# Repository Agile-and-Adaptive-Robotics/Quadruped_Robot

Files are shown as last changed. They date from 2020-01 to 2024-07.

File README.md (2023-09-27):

# AARL Quadruped Robot - Muscle Mutt

## Summary
This repository contains files relevant to the design, analysis, and testing of AARL's canine-inspired quadruped robot named Muscle Mutt.  Our goal in developing Muscle Mutt is for it to serve as a biologically relevant platform for testing embodied synthetic nervous systems pertaining to legged locomotion.  Toward this end, Muscle Mutt features body proportions similar to that of a Whippet, antagonistic pairs of braided pneumatic actuators (BPAs) that serve as proxies for muscles, and a CPG based neural control scheme.  All aspects of Muscle Mutt's design are under active development, including adjusting passive limb dynamics to be congruent with animal models, updating the electrical subsystem to incorporate a wider array of biologically relevant sensory feedback, and designing neural algorithms to generate stable and robust locomotion.

## References
More details on the design and testing of Muscle Mutt can be found in our associated papers.
```
@article{
C. W. Scharzenberger, “Design of a Canine Inspired Quadruped Robot as a Platform for Synthetic Neural Network Control,” Master’s Thesis, Portland State University, Digital, 2019. Accessed: Jun. 18, 2023. [Online]. Available: https://www.proquest.com/docview/2289587100?pq-origsite=gscholar&fromopenview=true
}
```
[Link to paper](https://pdxscholar.library.pdx.edu/cgi/viewcontent.cgi?article=6210&context=open_access_etds)

## Install Instructions
As a comprehensive robotics project, this repository contains information pertaining to three major areas of product development, including: (1) mechanical design, (2) electrical design, and (3) software.  The mechancial design for this project has been completed in Solidworks, while the electrical design has been completed in Eagle.  High level control software has primarily been developed in Matlab, though more recent efforts have been conducted in Python.  Requiste python modules are provided in requirement files in relevant directories.

## Repository Organization
This repository is organized into six primary directories, including: (1) Animatlab, (2) CAD_Electrical, (3) CAD_Mechanical, (4) Code, (5) Documentation, and (6) Manufacturing.  The names of these directories are largely self explanatory, with Animatlab neuromechanical simulations being stored in the Animatlab folder; Eagle CAD documents in the CAD_Electrical folder; Solidworks CAD documents in the CAD_Mechanical folder; Matlab, Python, and C code in the Code folder; supporting documentation and datasheets in the Documentation folder; and 3D printing documentation in the Manufacturing folder.

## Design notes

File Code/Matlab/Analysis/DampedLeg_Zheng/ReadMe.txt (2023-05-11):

FILE PATHS
Some folder names may have changed in an effort to clean up.
Data file and functions' locations may need to be re-established before running.

RAW DATA PROCESSING

Raw data files were too large to commit to GitHub but available upon request. 
Processed joint angle data is saved as Matlab data file "jdata".

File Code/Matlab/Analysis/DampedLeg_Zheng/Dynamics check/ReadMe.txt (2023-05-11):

OLD CODE
Contains troubleshooting code not actively used in analysis or old code that didn't work.

DYNAMICS CHECK CURRENT
Was used initially to create an animated display of a three link pendulum with given k,b,mu values

GEOMETRY CHECK
Was used in early phase of the project just to ensure center of masses and joint angles were defined correctly.

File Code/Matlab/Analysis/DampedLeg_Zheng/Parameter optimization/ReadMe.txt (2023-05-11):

DYNAMIC PROPERTIES CALC
Was used to calculate risetime in the hip, and frequency and damping ratio in the knee for rat trials so they did not need to be calculated at every iteration
Several different versions tried

IC_check
Main script is dynamic_IC_check.
Allows the user to enter values of friction (not used), k, and b.
User must enter a trial and muscle number to compare to.
Using IC from selected trial, ODE is run on system with selected parameters.
Joint angles over time are outputted and user has option to save. 

OPTIMIZER FUNCTIONS AND DATA
These are miscellaneous scripts need to run the optimizers.
Includes cost calculations, joint angle data, EOM, mechanical properties of the systems, etc.

OPTIMIZER SCRIPTS
Different optimization scripts
NOTE: Much of the code floating around this project has been copy and pasted from previous versions I've written, and some comments may contain errors
These had many changes and iterations, and the code gets a little sloppy in some places. Please contact me if there's any confusion.

RESULTS
Optimization results, sorted into folders.
Generally a data file and a figure are saved for each optimization.

TRIAL PLOTTING
Plotting of the rat leg trials used, as joint angle data over time.

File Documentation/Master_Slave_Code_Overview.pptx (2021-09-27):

## Master & Slave C Code Overview

March 25th, 2021

## Existing Hardware Organization

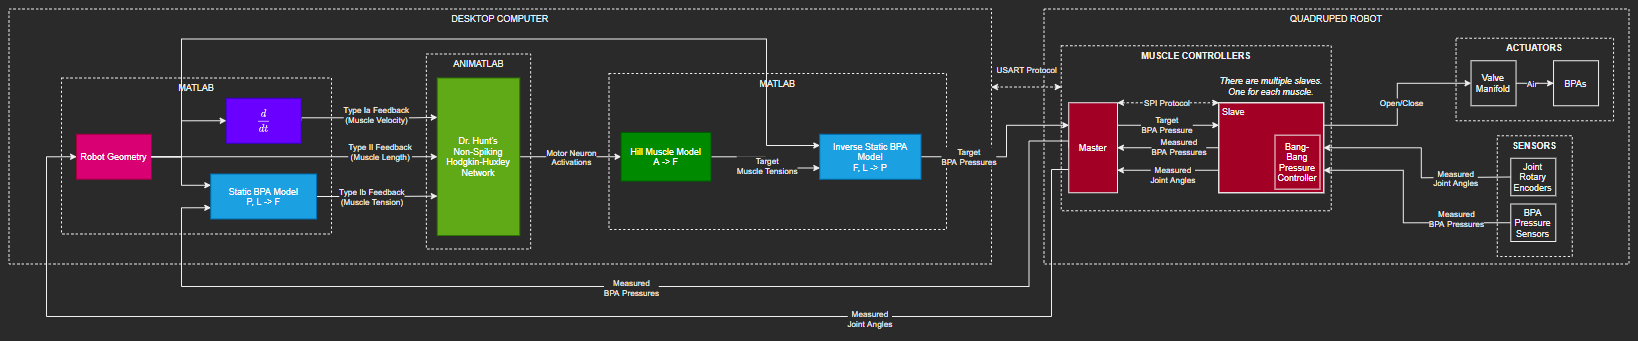
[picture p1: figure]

## Master Micro Duties

- Read desired muscle pressures from Matlab.
- Write desired muscle pressures to appropriate slave microcontrollers.
- Read sensor data from the slave microcontrollers.
- Write sensor data to Matlab.

## Master Micro approach

- Setup microcontroller in main function.
- In a timer interrupt, perform the required duties:
  - Read Matlab commands.
  - Write Slave commands.
  - Read Slave sensors.
  - Write Matlab sensors.
- Slave information is stored in a data structure: “slave manager”

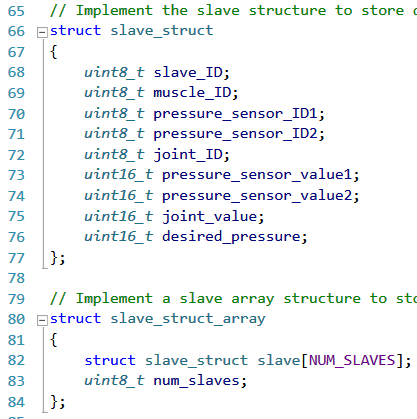
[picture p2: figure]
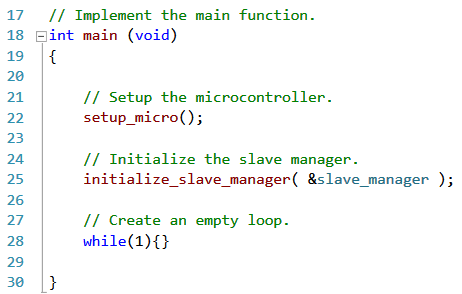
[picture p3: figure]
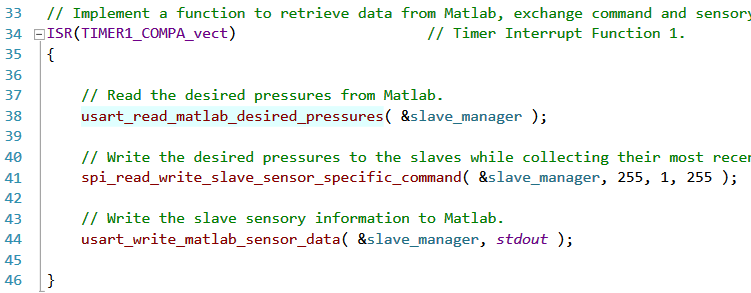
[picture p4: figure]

## A note about functions…

- Functions are stored in separate C files.
- Function files include:
  - Setup_Functions.c
  - SPI_Functions.c
  - USART_Functions.c
  - ADC_DAC_Functions.c
  - Conversion_Functions.c
  - Pin_Functions.c
  - Control Functions
  - Encoder Functions
- Master & Slave micros have their own versions of each of these files.

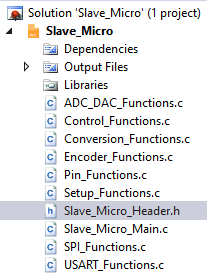
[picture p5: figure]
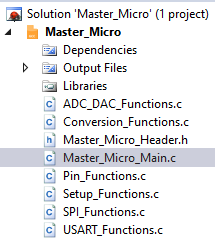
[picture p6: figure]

## Master Micro: Reading Matlab Commands

- Usart_read_matlab_desired_pressures
  - Waits for the “start sequence” from Matlab.
  - Reads the number of commands to expect.
  - Reads each set of command values.
  - Stores the desired pressure commands into the slave manager.

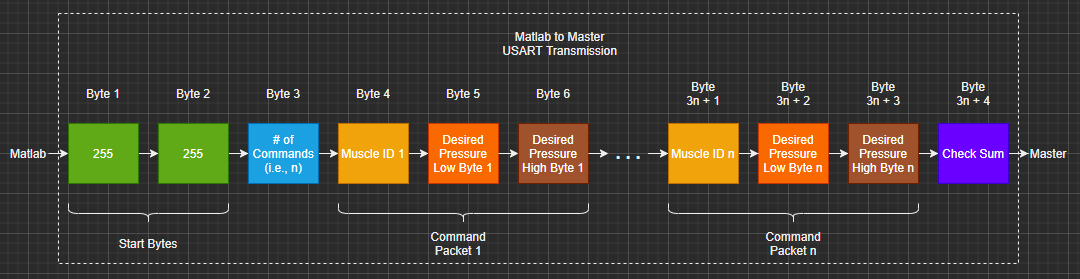
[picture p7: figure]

## Master Micro: Read / Write to Slaves

- Spi_read_write_slave_sensor_specific_command
  - Builds a byte array to send to the slave.
  - Writes the command ID.
  - Writes the sensor ID.
  - Writes the command low & high bytes.
  - Writes 4 more dummy bytes if we want to read all sensors from the slave.
  - Stores the received data in the slave manager.

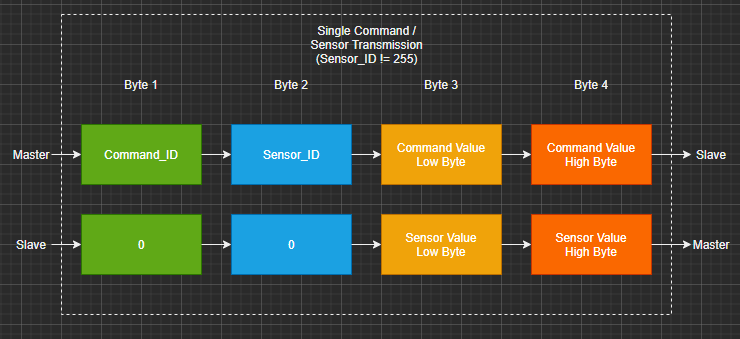
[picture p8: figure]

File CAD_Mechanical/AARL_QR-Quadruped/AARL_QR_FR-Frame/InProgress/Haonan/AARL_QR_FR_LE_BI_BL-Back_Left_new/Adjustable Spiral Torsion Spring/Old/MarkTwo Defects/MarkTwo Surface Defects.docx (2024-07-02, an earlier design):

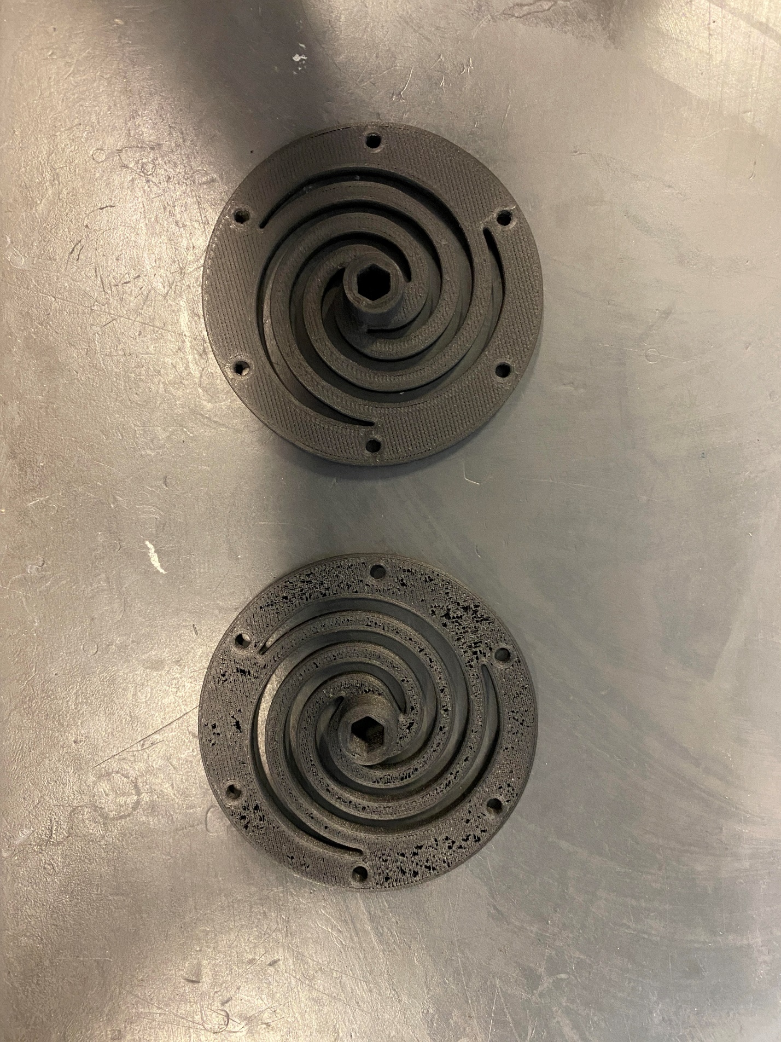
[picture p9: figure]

Top Surface

Mark Two

Onyx One

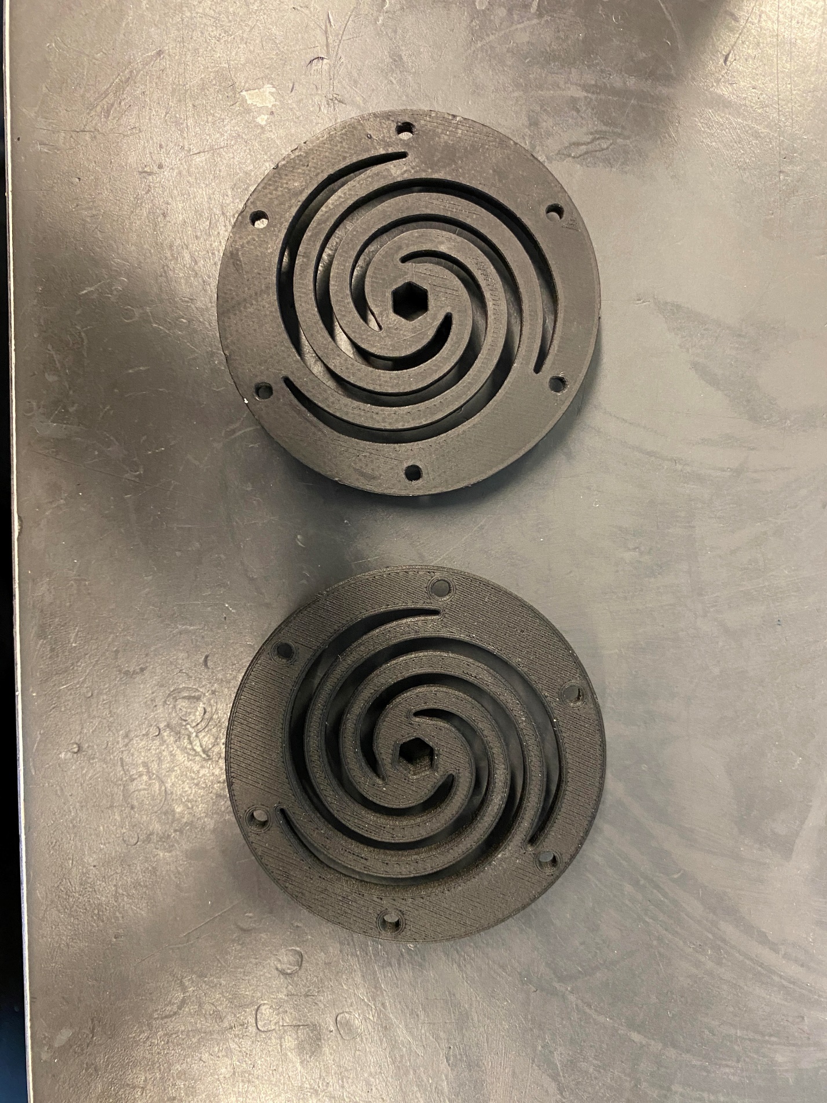
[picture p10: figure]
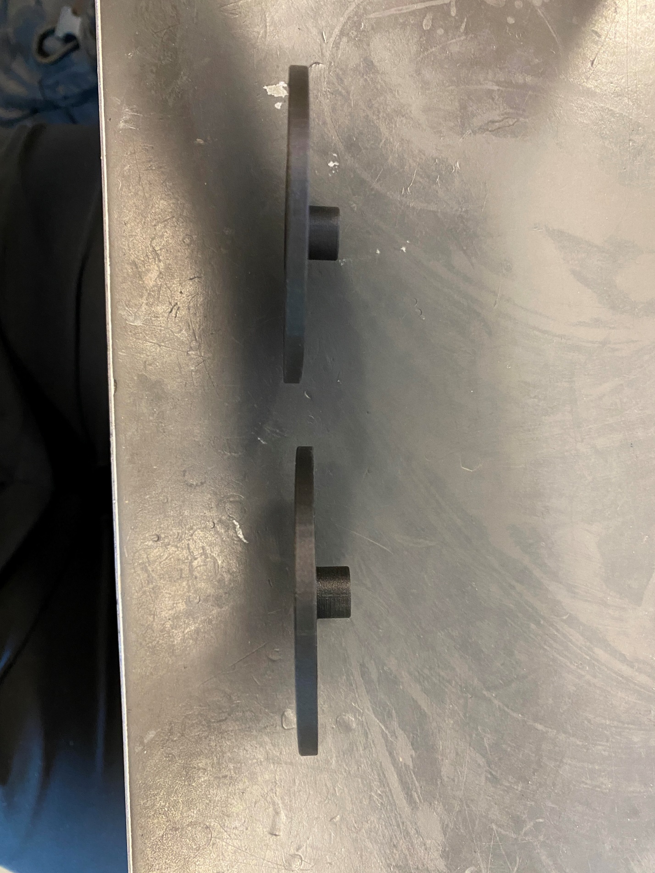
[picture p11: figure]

Bottom Surface

Onyx One

Mark Two

Side Walls

Mark Two

Onyx One

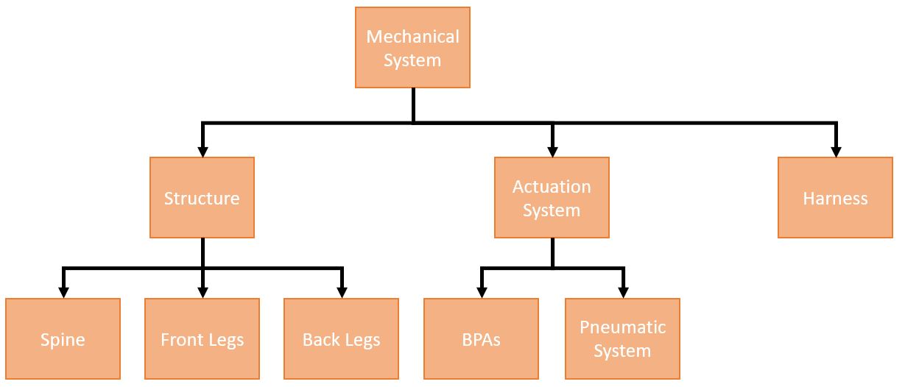
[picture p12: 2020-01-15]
Documentation/Pictures/PSU_Puppy_Pictures/Mechanical_Systems_Block_Diagram.JPG

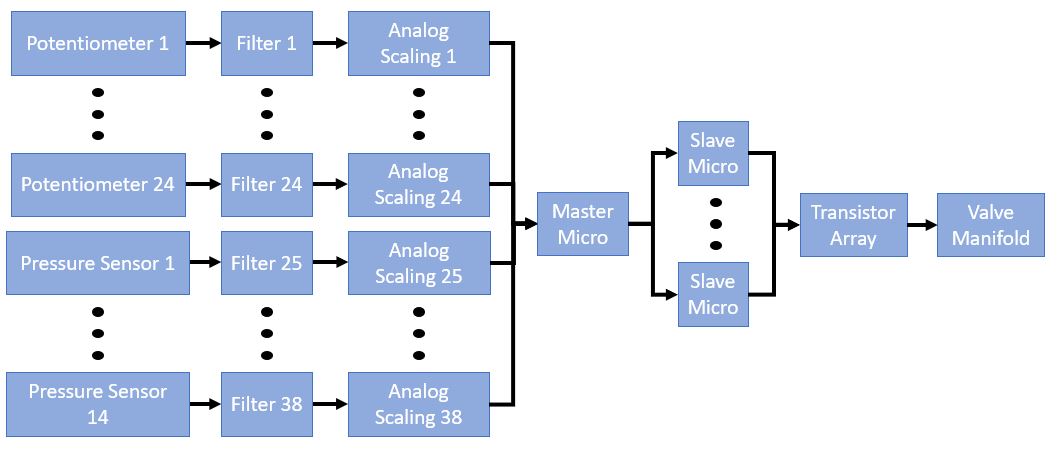
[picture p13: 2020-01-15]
Documentation/Pictures/PSU_Puppy_Pictures/Hardware_Flowchart.JPG

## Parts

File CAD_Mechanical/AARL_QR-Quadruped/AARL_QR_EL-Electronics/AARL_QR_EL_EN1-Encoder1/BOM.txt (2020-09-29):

3DX_CUI_DEVICES_Supplier: CUI Devices
3DX_CUI_DEVICES_Description: AMT10 Radial, Fixed Resolution, 500 PPR, Single Index Pulse, 4 mm Bore, Standard, Incremental, Capacitive Modular Encoder
3DX_CUI_DEVICES_Model Number: AMT102-0500-I4000-S

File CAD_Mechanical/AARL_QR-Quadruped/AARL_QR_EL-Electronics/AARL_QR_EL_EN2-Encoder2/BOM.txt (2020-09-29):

3DX_CUI_DEVICES_Supplier: CUI Devices
3DX_CUI_DEVICES_Description: AMT10 Radial, Fixed Resolution, 500 PPR, Single Index Pulse, 6.35 mm Bore, Standard, Incremental, Capacitive Modular Encoder
3DX_CUI_DEVICES_Model Number: AMT102-0500-I6350-S

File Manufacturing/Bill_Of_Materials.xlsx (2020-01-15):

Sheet: Bill Of Materials
ID | Name | Part # | Parent | Material Cost | Density | Unit Volume | Unit Mass | Unit Cost | Quantity | Total Mass | Total Cost | Quantity Owned | Quantity Needed | Manufacturing Method | Supplier | Link | Description | Notes
[#] | [-] | [-] | [-] | [$/cm^3] | [g/cm^3] | [cm^3/#] | [g/#] | [$/#] | [#] | [g] | [$] | [#] | [#] | [-] | [-] | [-] | [-] | [-]
1 | Center Cross Bar | AARL_Puppy_18_01_01_002 | Spine | 0.23625 | 1.2 | 24.4 | 29.28 | 5.7645 | 1 | 29.28 | 5.7645 | 0 | 1 | 3D Printing
2 | Front & Rear Cross Bar | AARL_Puppy_18_01_01_004 | Spine | 0.23625 | 1.2 | 18.2 | 21.84 | 4.29975 | 2 | 43.68 | 8.5995 | 0 | 2 | 3D Printing
3 | Front & Rear Cross Bar Insert | AARL_Puppy_18_01_01_005 | Spine | 0.23625 | 1.2 | 3.84 | 4.608 | 0.9072 | 4 | 18.432 | 3.6288 | 0 | 4 | 3D Printing
4 | Hip Potentiometer Bracket | AARL_Puppy_18_01_01_006 | Spine | 0.23625 | 1.2 | 6.48 | 7.776 | 1.5309 | 4 | 31.104 | 6.1236 | 0 | 4 | 3D Printing
5 | Middle Spine Section | AARL_Puppy_18_01_01_008 | Spine | 0.23625 | 1.2 | 258 | 309.6 | 60.9525 | 1 | 309.6 | 60.9525 | 0 | 1 | 3D Printing
6 | Outer Spine Section | AARL_Puppy_18_01_01_009 | Spine | 0.23625 | 1.2 | 224 | 268.8 | 52.92 | 2 | 537.6 | 105.84 | 0 | 2 | 3D Printing
7 | Ribbion Cable Bracket | AARL_Puppy_18_01_01_010 | Spine | 0.23625 | 1.2 | 9.39 | 11.268 | 2.2183875 | 1 | 11.268 | 2.2183875 | 0 | 1 | 3D Printing
8 | Air Supply Tubing Bracket | AARL_Puppy_18_01_01_011 | Spine | 0.23625 | 1.2 | 4.98 | 5.976 | 1.176525 | 1 | 5.976 | 1.176525 | 0 | 1 | 3D Printing
9 | Inside Piano Hinge Piece | AARL_Puppy_18_01_02_002 | Front Leg | 0.23625 | 1.2 | 5.74 | 6.888 | 1.356075 | 10 | 68.88 | 13.56075 | 0 | 10 | 3D Printing
10 | Standard Muscle Bracket (Small) | AARL_Puppy_18_01_02_003 | Front Leg | 0.23625 | 1.2 | 1.54 | 1.848 | 0.363825 | 18 | 33.264 | 6.54885 | 0 | 18 | 3D Printing
11 | Double Muscle Bracket (Center) | AARL_Puppy_18_01_02_005 | Front Leg | 0.23625 | 1.2 | 3.18 | 3.816 | 0.751275 | 2 | 7.632 | 1.50255 | 0 | 2 | 3D Printing
12 | Piano Hinge Potentiometer Piece | AARL_Puppy_18_01_02_009 | Front Leg | 0.23625 | 1.2 | 0.98 | 1.176 | 0.231525 | 10 | 11.76 | 2.31525 | 0 | 10 | 3D Printing
13 | Vishay Potentiometer | AARL_Puppy_18_01_02_013 | Electronics |  |  |  | 0 | 0 | 14 | 0 | 0 |  | 14 | Purchased | Vishay
14 | Bearing Insert | AARL_Puppy_18_01_02_014 | Front Leg | 0.23625 | 1.2 | 0.15 | 0.18 | 0.0354375 | 38 | 6.84 | 1.346625 | 0 | 38 | 3D Printing
15 | Outside Piano Hinge Piece | AARL_Puppy_18_01_02_015 | Front Leg | 0.23625 | 1.2 | 5.84 | 7.008 | 1.3797 | 10 | 70.08 | 13.797 | 0 | 10 | 3D Printing
16 | Foot Member | AARL_Puppy_18_01_02_016 | Front Leg | 0.23625 | 1.2 | 6.86 | 8.232 | 1.620675 | 4 | 32.928 | 6.4827 | 0 | 4 | 3D Printing
17 | Front Foot | AARL_Puppy_18_01_02_017 | Front Leg | 0.23625 | 1.2 | 4.2 | 5.04 | 0.99225 | 2 | 10.08 | 1.9845 | 0 | 2 | 3D Printing
18 | Back Hip Member | AARL_Puppy_18_01_02_018 | Front Leg | 0.23625 | 1.2 | 16.9 | 20.28 | 3.992625 | 2 | 40.56 | 7.98525 | 0 | 2 | 3D Printing
19 | Hip Potentiometer Piece | AARL_Puppy_18_01_02_021 | Front Leg | 0.23625 | 1.2 | 1.48 | 1.776 | 0.34965 | 4 | 7.104 | 1.3986 | 0 | 4 | 3D Printing
20 | Foot Cushioning Ball | AARL_Puppy_18_01_02_022 | Front Leg |  |  |  | 0 | 0 | 4 | 0 | 0 |  | 4 | Purchased
21 | Back Leg Double Short Double Bracket | AARL_Puppy_18_01_02_023 | Back Leg | 0.23625 | 1.2 | 3.3 | 3.96 | 0.779625 | 2 | 7.92 | 1.55925 | 0 | 2 | 3D Printing
22 | Back Leg Femur Member | AARL_Puppy_18_01_04_001 | Back Leg | 0.23625 | 1.2 | 22.08 | 26.496 | 5.2164 | 2 | 52.992 | 10.4328 | 0 | 2 | 3D Printing
23 | Back Leg Tibia Member | AARL_Puppy_18_01_04_011 | Back Leg | 0.23625 | 1.2 | 27.43 | 32.916 | 6.4803375 | 2 | 65.832 | 12.960675 | 0 | 2 | 3D Printing
24 | Back Foot | AARL_Puppy_18_01_04_017 | Back Leg | 0.23625 | 1.2 | 8.31 | 9.972 | 1.9632375 | 2 | 19.944 | 3.926475 | 0 | 2 | 3D Printing
25 | Back Leg Knee Bracket | AARL_Puppy_18_01_04_018 | Back Leg | 0.23625 | 1.2 | 8.29 | 9.948 | 1.9585125 | 2 | 19.896 | 3.917025 | 0 | 2 | 3D Printing
26 | Front Leg Femur Member | AARL_Puppy_18_01_06_001 | Front Leg | 0.23625 | 1.2 | 19.6 | 23.52 | 4.6305 | 2 | 47.04 | 9.261 | 0 | 2 | 3D Printing
27 | Front Leg Middle Member | AARL_Puppy_18_01_06_002 | Front Leg | 0.23625 | 1.2 | 23.4 | 28.08 | 5.52825 | 2 | 56.16 | 11.0565 | 0 | 2 | 3D Printing
28 | Front Leg Tibia | AARL_Puppy_18_01_06_004 | Front Leg | 0.23625 | 1.2 | 27.4 | 32.88 | 6.47325 | 2 | 65.76 | 12.9465 | 0 | 2 | 3D Printing
29 | Standard Muscle Bracket (Medium) | AARL_Puppy_18_01_06_005 | Front Leg | 0.23625 | 1.2 | 2.22 | 2.664 | 0.524475 | 6 | 15.984 | 3.14685 | 0 | 6 | 3D Printing
30 | Front Leg Pantograph Member | AARL_Puppy_18_01_06_006 | Front Leg | 0.23625 | 1.2 | 19 | 22.8 | 4.48875 | 2 | 45.6 | 8.9775 | 0 | 2 | 3D Printing
31 | Front Leg Double Knee Bracket | AARL_Puppy_18_01_06_008 | Front Leg | 0.23625 | 1.2 | 9.19 | 11.028 | 2.1711375 | 2 | 22.056 | 4.342275 | 0 | 2 | 3D Printing
32 | Front / Back Leg Knee Bracket | AARL_Puppy_18_01_06_010 | Front Leg | 0.23625 | 1.2 | 7.95 | 9.54 | 1.8781875 | 6 | 57.24 | 11.269125 | 0 | 6 | 3D Printing
33 | Front Hip Member | AARL_Puppy_18_01_06_011 | Front Leg | 0.23625 | 1.2 | 18.6 | 22.32 | 4.39425 | 2 | 44.64 | 8.7885 | 0 | 2 | 3D Printing
34 | Front Leg Top Offset Bracket | AARL_Puppy_18_01_06_012 | Front Leg | 0.23625 | 1.2 | 3.46 | 4.152 | 0.817425 | 2 | 8.304 | 1.63485 | 0 | 2 | 3D Printing
35 | Standard Potentiometer Mounting Bracket | AARL_Puppy_18_01_06_013 | Front Leg | 0.23625 | 1.2 | 2.45 | 2.94 | 0.5788125 | 10 | 29.4 | 5.788125 | 0 | 10 | 3D Printing
36 | Front Leg Bottom Offset Bracket | AARL_Puppy_18_01_06_014 | Front Leg | 0.23625 | 1.2 | 4.32 | 5.184 | 1.0206 | 2 | 10.368 | 2.0412 | 0 | 2 | 3D Printing
37 | Muscle String Tie Down | AARL_Puppy_18_01_09_004 | Muscle | 0.23625 | 1.2 | 2.27 | 2.724 | 0.5362875 | 24 | 65.376 | 12.8709 | 0 | 24 | 3D Printing
38 | Muscle Insert with Pneumatic Connection | AARL_Puppy_18_02_01_002 | Muscle | 0.23625 | 1.2 | 2.78 | 3.336 | 0.656775 | 24 | 80.064 | 15.7626 | 0 | 24 | 3D Printing
39 | QSML-M3-4 | AARL_Puppy_18_02_01_004 | Muscle |  |  |  | 0 | 0 | 24 | 0 | 0 |  | 24 | Purchased | Festo
40 | Hose Clamp | AARL_Puppy_18_02_01_005 | Pneumatics |  |  |  | 0 | 0 | 48 | 0 | 0 |  | 48 | Purchased
41 | Muscle Tie Down Insert | AARL_Puppy_18_02_01_007 | Muscle | 0.23625 | 1.2 | 2.53 | 3.036 | 0.5977125 | 24 | 72.864 | 14.3451 | 0 | 24 | 3D Printing
42 | VTUG-10-MRCR-S1TZ-26V20-T516-UL-M5S-12K | AARL_Puppy_18_02_31_000 | Pneumatics |  |  |  | 0 | 0 | 1 | 0 | 0 |  | 1 | Purchased | Festo
43 | QSL-G1/8-8 | AARL_Puppy_18_02_57_003 | Fitting |  |  |  | 0 | 0 | 1 | 0 | 0 |  | 1 | Purchased | Festo
44 | QSLV-M5-6 | AARL_Puppy_18_02_57_004 | Fitting |  |  |  | 0 | 0 | 1 | 0 | 0 |  | 1 | Purchased | Festo
45 | QSL-8 | AARL_Puppy_18_02_57_006 | Fitting |  |  |  | 0 | 0 | 1 | 0 | 0 |  | 1 | Purchased | Festo
46 | QSML-6 | AARL_Puppy_18_02_57_005 | Fitting |  |  |  | 0 | 0 | 1 | 0 | 0 |  | 1 | Purchased | Festo
47 | QSML-4 | AARL_Puppy_18_02_57_002 | Fitting |  |  |  | 0 | 0 | 48 | 0 | 0 |  | 48 | Purchased | Festo
48 | QSM-6-4 | AARL_Puppy_18_02_57_001 | Fitting |  |  |  | 0 | 0 | 24 | 0 | 0 |  | 24 | Purchased | Festo
49 | QSMT-4 | AARL_Puppy_18_02_57_007 | Fitting |  |  |  | 0 | 0 | 24 | 0 | 0 |  | 24 | Purchased | Festo
50 | Pressure Sensor Case | AARL_Puppy_18_03_03_001 | Electronics | 0.23625 | 1.2 | 109.88 | 131.856 | 25.95915 | 1 | 131.856 | 25.95915 | 0 | 1 | 3D Printing
51 | Pressure Sensor Case Lid | AARL_Puppy_18_03_03_002 | Electronics | 0.23625 | 1.2 | 40.22 | 48.264 | 9.501975 | 1 | 48.264 | 9.501975 | 0 | 1 | 3D Printing
52 | Pressure Sensor - MPX5700GP | AARL_Puppy_18_03_01_002 | Electronics |  |  |  | 0 | 0 | 24 | 0 | 0 |  | 24 | Purchased
53 | Solderable Breadboard | AARL_Puppy_18_03_01_009 | Electronics |  |  |  | 0 | 0 | 4 | 0 | 0 |  | 4 | Purchased
54 | Pressure Sensor Spacer | AARL_Puppy_18_03_01_010 | Electronics | 0.23625 | 1.2 | 0.09 | 0.108 | 0.0212625 | 48 | 5.184 | 1.0206 | 0 | 48 | 3D Printing
55 | Pressure Sensor Ribbon Cable Connector (46 Pin) | AARL_Puppy_18_03_05_002 | Electronics |  |  |  | 0 | 0 | 1 | 0 | 0 |  | 1 | Purchased
56 | Pressure Sensor Ribbon Cable (46 Pin) | AARL_Puppy_18_03_05_001 | Electronics |  |  |  | 0 | 0 | 2 | 0 | 0 |  | 2 | Purchased
57 | Electronics Input Connector |  | Electronics |  |  |  | 0 | 0 | 2 | 0 | 0 |  | 2 | Purchased |  |  |  | Still needs to be modeled.
58 | Electronics Input Ribbon Cable |  | Electronics |  |  |  | 0 | 0 | 2 | 0 | 0 |  | 2 | Purchased |  |  |  | Still needs to be modeled.
59 | #4-40x0.0625 Set Screw | AARL_Puppy_18_04_02_001 | Fastener |  |  |  | 0 | 0 | 28 | 0 | 0 |  | 28 | Purchased
60 | #4-40x0.25 SHCS | AARL_Puppy_18_04_01_004 | Fastener |  |  |  | 0 | 0 | 144 | 0 | 0 |  | 144 | Purchased
61 | #4-40x0.28125 SHCS | AARL_Puppy_18_04_01_005 | Fastener |  |  |  | 0 | 0 | 28 | 0 | 0 |  | 28 | Purchased
62 | #4-40x0.375 SHCS | AARL_Puppy_18_04_01_009 | Fastener |  |  |  | 0 | 0 | 18 | 0 | 0 |  | 18 | Purchased
63 | #4-40x2.5 SHCS | AARL_Puppy_18_04_01_014 | Fastener |  |  |  | 0 | 0 | 8 | 0 | 0 |  | 8 | Purchased
64 | #4-40 Nut | AARL_Puppy_18_04_07_002 | Fastener |  |  |  | 0 | 0 | 8 | 0 | 0 |  | 8 | Purchased
65 | #8-32x0.25 SHCS | AARL_Puppy_18_04_01_006 | Fastener |  |  |  | 0 | 0 | 38 | 0 | 0 |  | 38 | Purchased
66 | #8-32x0.75 SHCS | AARL_Puppy_18_04_01_007 | Fastener |  |  |  | 0 | 0 | 10 | 0 | 0 |  | 10 | Purchased
67 | #8-32x1.00 SHCS | AARL_Puppy_18_04_01_008 | Fastener |  |  |  | 0 | 0 | 4 | 0 | 0 |  | 4 | Purchased
68 | #8-32x1.25 SHSS | AARL_Puppy_18_04_01_013 | Fastener |  |  |  | 0 | 0 | 4 | 0 | 0 |  | 4 | Purchased
69 | 1/4-20x0.375 SHCS | AARL_Puppy_18_04_01_002 | Fastener |  |  |  | 0 | 0 | 6 | 0 | 0 |  | 6 | Purchased
70 | 1/4x0.75 Chicago Screw (Female) | AARL_Puppy_18_04_09_001 | Fastener |  |  |  | 0 | 0 | 52 | 0 | 0 |  | 52 | Purchased
71 | 1/4x0.75 Chicago Screw (Male) | AARL_Puppy_18_04_09_002 | Fastener |  |  |  | 0 | 0 | 52 | 0 | 0 |  | 52 | Purchased
72 | 1/4-20 Nut | AARL_Puppy_18_04_07_001 | Fastener |  |  |  | 0 | 0 | 14 | 0 | 0 |  | 14 | Purchased
73 | 1/8 ID Plastic Washer | AARL_Puppy_18_04_06_002 | Fastener |  |  |  | 0 | 0 | 16 | 0 | 0 |  | 16 | Purchased
74 | 3/32 Plastic Spacer | AARL_Puppy_18_04_06_001 | Fastener |  |  |  | 0 | 0 | 16 | 0 | 0 |  | 16 | Purchased
75 | 1/4 ID Roller Bearing | AARL_Puppy_18_04_03_001 | Fastener |  |  |  | 0 | 0 | 8 | 0 | 0 |  | 8 | Purchased
76 | String | AARL_Puppy_18_01_09_005 | Fastener |  |  |  | 0 | 0 | 1 | 0 | 0 |  | 1 | Purchased |  |  | 44.5322 inches required. | Many different models. No specific part number.
77 | M4 Tubing | AARL_Puppy_18_02_32_084 | Pneumatics |  |  |  | 0 | 0 | 1 | 0 | 0 |  | 1 | Purchased | Festo |  | 85.36159 feet required. | Many different models. No specific part number.
78 | M6 Tubing | AARL_Puppy_18_02_32_083 | Pneumatics |  |  |  | 0 | 0 | 1 | 0 | 0 |  | 1 | Purchased | Festo |  | 31.0577 inches required. | Many different models. No specific part number.
79 | M8 Tubing | AARL_Puppy_18_02_32_081 | Pneumatics |  |  |  | 0 | 0 | 1 | 0 | 0 |  | 1 | Purchased | Festo |  | 3.0571 inches required. | Many different models. No specific part number.
80 | Pneumatic Muscles | AARL_Puppy_18_02_33_001 | Pneumatics |  |  |  | 0 | 0 | 1 | 0 | 0 |  | 1 | Purchased | Festo |  | 122.875 inches required. | Many different models. No specific part number.
 |  |  |  |  |  |  |  |  |  | 2248.812

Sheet: Manufacturing Plan
Back Leg
ID | Name | Part # | Parent | Material Cost | Density | Unit Volume | Unit Mass | Unit Cost | Subassembly Quantity | Total Quantity | Total Mass | Total Cost | Notes
[#] | [-] | [-] | [-] | [$/cm^3] | [g/cm^3] | [cm^3/#] | [g/#] | [$/#] | [#] | [#] | [g] | [$] | [-]
1 | Single Muscle Bracket (Small) | AARL_Puppy_18_01_02_003 | Front Leg / Back Leg / Spine | 0.23625 | 1.2 | 1.54 | 1.848 | 0.363825 | 4 | 18 | 33.264 | 6.54885 | This part needs to be redesigned to avoid cracking down the middle where the mounting holes are located. Could potentially be replaced by the medium single muscle bracket.
2 | Single Muscle Bracket (Medium) | AARL_Puppy_18_01_06_005 | Front Leg / Back Leg | 0.23625 | 1.2 | 2.22 | 2.664 | 0.524475 | 1 | 6 | 15.984 | 3.14685
3 | Double Muscle Bracket (Short) | AARL_Puppy_18_01_02_023 | Back Leg | 0.23625 | 1.2 | 3.3 | 3.96 | 0.779625 | 1 | 2 | 7.92 | 1.55925
4 | Double Muscle Bracket (Medium) | AARL_Puppy_18_01_04_018 | Back Leg | 0.23625 | 1.2 | 8.29 | 9.948 | 1.9585125 | 1 | 2 | 19.896 | 3.917025
5 | Single Muscle Bracket (Long) | AARL_Puppy_18_01_06_010 | Front Leg / Back Leg | 0.23625 | 1.2 | 7.95 | 9.54 | 1.8781875 | 1 | 6 | 57.24 | 11.269125
6 | Standard Potentiometer Mounting Bracket | AARL_Puppy_18_01_06_013 | Front Leg / Back Leg | 0.23625 | 1.2 | 2.45 | 2.94 | 0.5788125 | 2 | 10 | 29.4 | 5.788125
7 | Hip Potentiometer Piece | AARL_Puppy_18_01_02_021 | Front Leg / Back Leg | 0.23625 | 1.2 | 1.48 | 1.776 | 0.34965 | 1 | 4 | 7.104 | 1.3986
8 | Bearing Insert | AARL_Puppy_18_01_02_014 | Front Leg / Back Leg | 0.23625 | 1.2 | 0.15 | 0.18 | 0.0354375 | 9 | 38 | 6.84 | 1.346625
9 | Inside Piano Hinge Piece | AARL_Puppy_18_01_02_002 | Front Leg / Back Leg | 0.23625 | 1.2 | 5.74 | 6.888 | 1.356075 | 2 | 10 | 68.88 | 13.56075
10 | Outside Piano Hinge Piece | AARL_Puppy_18_01_02_015 | Front Leg / Back Leg | 0.23625 | 1.2 | 5.84 | 7.008 | 1.3797 | 2 | 10 | 70.08 | 13.797
11 | Piano Hinge Potentiometer Piece | AARL_Puppy_18_01_02_009 | Front Leg / Back Leg | 0.23625 | 1.2 | 0.98 | 1.176 | 0.231525 | 2 | 10 | 11.76 | 2.31525
12 | Back Hip Member | AARL_Puppy_18_01_02_018 | Back Leg | 0.23625 | 1.2 | 16.9 | 20.28 | 3.992625 | 1 | 2 | 40.56 | 7.98525
13 | Back Leg Femur Member | AARL_Puppy_18_01_04_001 | Back Leg | 0.23625 | 1.2 | 22.08 | 26.496 | 5.2164 | 1 | 2 | 52.992 | 10.4328
14 | Back Leg Tibia Member | AARL_Puppy_18_01_04_011 | Back Leg | 0.23625 | 1.2 | 27.43 | 32.916 | 6.4803375 | 1 | 2 | 65.832 | 12.960675
15 | Foot Member | AARL_Puppy_18_01_02_016 | Front Leg / Back Leg | 0.23625 | 1.2 | 6.86 | 8.232 | 1.620675 | 1 | 4 | 32.928 | 6.4827
16 | Back Foot | AARL_Puppy_18_01_04_017 | Back Leg | 0.23625 | 1.2 | 8.31 | 9.972 | 1.9632375 | 1 | 2 | 19.944 | 3.926475 | This part may be too long and weak.
Front Leg
ID | Name | Part # | Parent | Material Cost | Density | Unit Volume | Unit Mass | Unit Cost | Subassembly Quantity | Total Quantity | Total Mass | Total Cost | Notes
[#] | [-] | [-] | [-] | [$/cm^3] | [g/cm^3] | [cm^3/#] | [g/#] | [$/#] | [#] | [#] | [g] | [$] | [-]
1 | Single Muscle Bracket (Small) | AARL_Puppy_18_01_02_003 | Front Leg / Back Leg / Spine | 0.23625 | 1.2 | 1.54 | 1.848 | 0.363825 | 3 | 18 | 33.264 | 6.54885
2 | Single Muscle Bracket (Medium) | AARL_Puppy_18_01_06_005 | Front Leg / Back Leg | 0.23625 | 1.2 | 2.22 | 2.664 | 0.524475 | 2 | 6 | 15.984 | 3.14685
3 | Single Muscle Bracket (Long) | AARL_Puppy_18_01_06_010 | Front Leg / Back Leg | 0.23625 | 1.2 | 7.95 | 9.54 | 1.8781875 | 2 | 6 | 57.24 | 11.269125
4 | Standard Potentiometer Mounting Bracket | AARL_Puppy_18_01_06_013 | Front Leg / Back Leg | 0.23625 | 1.2 | 2.45 | 2.94 | 0.5788125 | 3 | 10 | 29.4 | 5.788125
5 | Hip Potentiometer Piece | AARL_Puppy_18_01_02_021 | Front Leg / Back Leg | 0.23625 | 1.2 | 1.48 | 1.776 | 0.34965 | 1 | 4 | 7.104 | 1.3986
6 | Bearing Insert | AARL_Puppy_18_01_02_014 | Front Leg / Back Leg | 0.23625 | 1.2 | 0.15 | 0.18 | 0.0354375 | 11 | 38 | 6.84 | 1.346625
7 | Inside Piano Hinge Piece | AARL_Puppy_18_01_02_002 | Front Leg / Back Leg | 0.23625 | 1.2 | 5.74 | 6.888 | 1.356075 | 3 | 10 | 68.88 | 13.56075
8 | Outside Piano Hinge Piece | AARL_Puppy_18_01_02_015 | Front Leg / Back Leg | 0.23625 | 1.2 | 5.84 | 7.008 | 1.3797 | 3 | 10 | 70.08 | 13.797
9 | Piano Hinge Potentiometer Piece | AARL_Puppy_18_01_02_009 | Front Leg / Back Leg | 0.23625 | 1.2 | 0.98 | 1.176 | 0.231525 | 3 | 10 | 11.76 | 2.31525
10 | Foot Member | AARL_Puppy_18_01_02_016 | Front Leg / Back Leg | 0.23625 | 1.2 | 6.86 | 8.232 | 1.620675 | 1 | 4 | 32.928 | 6.4827
11 | Double Muscle Bracket (Long) | AARL_Puppy_18_01_06_008 | Front Leg | 0.23625 | 1.2 | 9.19 | 11.028 | 2.1711375 | 1 | 2 | 22.056 | 4.342275
12 | Front Leg Top Offset Bracket | AARL_Puppy_18_01_06_012 | Front Leg | 0.23625 | 1.2 | 3.46 | 4.152 | 0.817425 | 1 | 2 | 8.304 | 1.63485
13 | Front Leg Bottom Offset Bracket | AARL_Puppy_18_01_06_014 | Front Leg | 0.23625 | 1.2 | 4.32 | 5.184 | 1.0206 | 1 | 2 | 10.368 | 2.0412
14 | Front Hip Member | AARL_Puppy_18_01_06_011 | Front Leg | 0.23625 | 1.2 | 18.6 | 22.32 | 4.39425 | 1 | 2 | 44.64 | 8.7885
15 | Front Leg Femur Member | AARL_Puppy_18_01_06_001 | Front Leg | 0.23625 | 1.2 | 19.6 | 23.52 | 4.6305 | 1 | 2 | 47.04 | 9.261
16 | Front Leg Middle Member | AARL_Puppy_18_01_06_002 | Front Leg | 0.23625 | 1.2 | 23.4 | 28.08 | 5.52825 | 1 | 2 | 56.16 | 11.0565
17 | Front Leg Tibia | AARL_Puppy_18_01_06_004 | Front Leg | 0.23625 | 1.2 | 27.4 | 32.88 | 6.47325 | 1 | 2 | 65.76 | 12.9465
18 | Front Leg Pantograph Member | AARL_Puppy_18_01_06_006 | Front Leg | 0.23625 | 1.2 | 19 | 22.8 | 4.48875 | 1 | 2 | 45.6 | 8.9775
19 | Front Foot | AARL_Puppy_18_01_02_017 | Front Leg | 0.23625 | 1.2 | 4.2 | 5.04 | 0.99225 | 1 | 2 | 10.08 | 1.9845
Muscles
ID | Name | Part # | Parent | Material Cost | Density | Unit Volume | Unit Mass | Unit Cost | Subassembly Quantity | Total Quantity | Total Mass | Total Cost | Notes
[#] | [-] | [-] | [-] | [$/cm^3] | [g/cm^3] | [cm^3/#] | [g/#] | [$/#] | [#] | [#] | [g] | [$] | [-]
1 | Muscle String Tie Down | AARL_Puppy_18_01_09_004 | Muscle | 0.23625 | 1.2 | 2.27 | 2.724 | 0.5362875 | 1 | 24 | 65.376 | 12.8709 | Make string holes larger.
2 | Muscle Insert with Pneumatic Connection | AARL_Puppy_18_02_01_002 | Muscle | 0.23625 | 1.2 | 2.78 | 3.336 | 0.656775 | 1 | 24 | 80.064 | 15.7626
3 | Muscle Tie Down Insert | AARL_Puppy_18_02_01_007 | Muscle | 0.23625 | 1.2 | 2.53 | 3.036 | 0.5977125 | 1 | 24 | 72.864 | 14.3451 | Make string holes larger.
Electronics Housing
ID | Name | Part # | Parent | Material Cost | Density | Unit Volume | Unit Mass | Unit Cost | Subassembly Quantity | Total Quantity | Total Mass | Total Cost | Notes
[#] | [-] | [-] | [-] | [$/cm^3] | [g/cm^3] | [cm^3/#] | [g/#] | [$/#] | [#] | [#] | [g] | [$] | [-]
1 | Pressure Sensor Case | AARL_Puppy_18_03_03_001 | Electronics | 0.23625 | 1.2 | 109.88 | 131.856 | 25.95915 | 1 | 1 | 131.856 | 25.95915 | Move screw holes for lid mounting in to give them more meat.
2 | Pressure Sensor Case Lid | AARL_Puppy_18_03_03_002 | Electronics | 0.23625 | 1.2 | 40.22 | 48.264 | 9.501975 | 1 | 1 | 48.264 | 9.501975 | Move screw holes for lid mounting in to give them more meat.
3 | Pressure Sensor Spacer | AARL_Puppy_18_03_01_010 | Electronics | 0.23625 | 1.2 | 0.09 | 0.108 | 0.0212625 | 48 | 48 | 5.184 | 1.0206 | Move screw holes for lid mounting in to give them more meat.
Spine
ID | Name | Part # | Parent | Material Cost | Density | Unit Volume | Unit Mass | Unit Cost | Subassembly Quantity | Total Quantity | Total Mass | Total Cost | Notes
[#] | [-] | [-] | [-] | [$/cm^3] | [g/cm^3] | [cm^3/#] | [g/#] | [$/#] | [#] | [#] | [g] | [$] | [-]
1 | Single Muscle Bracket (Small) | AARL_Puppy_18_01_02_003 | Front Leg / Back Leg / Spine | 0.23625 | 1.2 | 1.54 | 1.848 | 0.363825 | 4 | 18 | 33.264 | 6.54885
1 | Double Muscle Bracket (Short) | AARL_Puppy_18_01_02_005 | Spine | 0.23625 | 1.2 | 3.18 | 3.816 | 0.751275 | 2 | 2 | 7.632 | 1.50255
9 | Air Supply Tubing Bracket | AARL_Puppy_18_01_01_011 | Spine | 0.23625 | 1.2 | 4.98 | 5.976 | 1.176525 | 1 | 1 | 5.976 | 1.176525
2 | Ribbion Cable Bracket | AARL_Puppy_18_01_01_010 | Spine | 0.23625 | 1.2 | 9.39 | 11.268 | 2.2183875 | 1 | 1 | 11.268 | 2.2183875 | Too fragile to bending. Need support material to prevent bending.
3 | Center Cross Bar | AARL_Puppy_18_01_01_002 | Spine | 0.23625 | 1.2 | 24.4 | 29.28 | 5.7645 | 1 | 1 | 29.28 | 5.7645
4 | Front & Rear Cross Bar | AARL_Puppy_18_01_01_004 | Spine | 0.23625 | 1.2 | 18.2 | 21.84 | 4.29975 | 2 | 2 | 43.68 | 8.5995
5 | Front & Rear Cross Bar Insert | AARL_Puppy_18_01_01_005 | Spine | 0.23625 | 1.2 | 3.84 | 4.608 | 0.9072 | 4 | 4 | 18.432 | 3.6288
6 | Hip Potentiometer Bracket | AARL_Puppy_18_01_01_006 | Spine | 0.23625 | 1.2 | 6.48 | 7.776 | 1.5309 | 4 | 4 | 31.104 | 6.1236
7 | Middle Spine Section | AARL_Puppy_18_01_01_008 | Spine | 0.23625 | 1.2 | 258 | 309.6 | 60.9525 | 1 | 1 | 309.6 | 60.9525
8 | Outer Spine Section | AARL_Puppy_18_01_01_009 | Spine | 0.23625 | 1.2 | 224 | 268.8 | 52.92 | 2 | 2 | 537.6 | 105.84

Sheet: Inventory
ID | Name | Part # | Parent | Quantity Owned | Supplier | Notes | Link
[#] | [-] | [-] | [-] | [#] | [-] | [-] | [-]
1 | Size 1'' Oetiker Stepless Ear Clamps, Single Ear Hose Clamps | AARL_Puppy_18_02_01_005 | Pneumatics | 10 | Murray |  | https://www.murraycorp.com/products/clamps/?_vsrefdom=ppcgoogle
2 | 1 3/16'' Cambridge Standard Hose Clamps | AARL_Puppy_18_02_01_005 | Pneumatics | 20 | Cambridge |  | http://www.cambridgeresources.com/products/c-12-standardhoseclamps/p-274-series2300
3 | One Ear Oetiker Clamp 133 for 7/16 OD Hose | AARL_Puppy_18_02_01_005 | Pneumatics | 46 | Murray |  | https://www.homebrewing.org/One-Ear-Oetiker-Clamp-133-Size-For-716-OD-Hose--100-Count_p_917.html
4 | Oetiker 15.7mm Clamp | AARL_Puppy_18_02_01_005 | Pneumatics | 3 | Murray |  | https://www.amazon.com/Oetiker-Stepless%C2%AE-Clamps-Single-Available/dp/B00ZJFWAK4
5 | Breeze Hose Clamp (Small) | AARL_Puppy_18_02_01_005 | Pneumatics | 26 | Breeze |  | http://www.breezehoseclamps.com/breeze/mini/
6 | M8 Tubing | AARL_Puppy_18_02_32_081 | Pneumatics | 1 | Festo | 3.0571 inches required. Estimated ~100 feet owned. Order Code: PUN-8X1,25-SI
7 | 1/4 Tubing |  | Pneumatics | 2 |  | ~100 feet each.
8 | 6mm x R1/4 Nitra Straight Fitting |  | Fitting | 20 | Nitra |  | https://www.automationdirect.com/adc/Overview/Catalog/Pneumatic_Components/Push-to-Connect_R-Thread_Pneumatic_Fittings_(Thermoplastic)/Male_Straight_(Round_Bo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
9 | Urbest ~6mm x ? Threaded Straight Fitting |  | Fitting | 20 | Urbest
10 | 1/4 x 5/16 Straight Fitting |  | Fitting | 5 | Mettle Air
11 | 1/4 T Fitting |  | Fitting | 20 | HFX
12 | 1/4 Y Fitting |  | Fitting | 20 | HFX
13 | 1/4 x 5/16? Thread L Fitting |  | Fitting | 3 | Mettle Air
14 | M4? Thread x 1/4 Straight Fitting |  | Fitting | 6 | Mettle Air
15 | POT 100 kOhm 1/5W Plastic Linear |  | Electronics | 25 | Digikey
16 | Pressure Sensor - MPX5700GP | AARL_Puppy_18_03_01_002 | Electronics | 32 | Digikey
17 | 1/4-20 Nut | AARL_Puppy_18_04_07_001 | Fastener | 25 | Digikey
18 | String | AARL_Puppy_18_01_09_005 | Fastener | 1 |  | 44.5322 inches required.

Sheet: Purchase Plan
ID | Name | Part # | Parent | Unit Cost | Quantity | Total Cost | Supplier | Notes | Link
[#] | [-] | [-] | [-] | [$/#] | [#] | [$] | [-] | [-] | [-]
1 | Foot Cushioning Ball | AARL_Puppy_18_01_02_022 | Front Leg |  | 4 | 0
2 | VTUG-10-MRCR-S1TZ-26V20-Q8LA-UL-M5S-12K | AARL_Puppy_18_02_31_000, Needs to be updated for new fitting sizes. | Pneumatics | 1505.86 | 1 | 1505.86 | Festo | Order Code: VTUG-10-MRCR-S1TZ-26V20-Q8LA-UL-M5S-12K | https://www.festo.com/cat/en-us_us/products_VTUG | Could get this later.
3 | M4 Tubing | AARL_Puppy_18_02_32_084 | Pneumatics | 36.5 | 1 | 36.5 | Festo | Order Code: PUN-4X0,75-SI, 50m Pack | https://www.festo.com/cat/en-us_us/products_PUN
4 | QSML-M3-4 | AARL_Puppy_18_02_01_004, Needs to be updated from M3 to M5. | Fitting | 45.8 | 3 | 137.4 | Festo | Order Code: QSML-M3-4, 10 Pc. Pack | https://www.festo.com/cat/en-us_us/products_QSM
5 | QSL-G1/8-8 | AARL_Puppy_18_02_57_003 | Fitting | 3.67 | 1 | 3.67 | Festo | Order Code: QSL-G1/8-8, each | https://www.festo.com/cat/en-us_us/products_QS
6 | QSLV-M5-6 | AARL_Puppy_18_02_57_004 | Fitting | 4.36 | 1 | 4.36 | Festo | Order Code: QSLV-M5-6, each | https://www.festo.com/cat/en-us_us/products_QS
7 | QSL-8 | AARL_Puppy_18_02_57_006 | Fitting | 35.2 | 1 | 35.2 | Festo | Order Code: QSL-8, 10 Pc. Pack | https://www.festo.com/cat/en-us_us/products_QS
8 | QSML-6 | AARL_Puppy_18_02_57_005 | Fitting | 30.7 | 1 | 30.7 | Festo | Order Code: QSML-6, 10 Pc. Pack | https://www.festo.com/cat/en-us_us/products_QSM
9 | QSML-4 | AARL_Puppy_18_02_57_002 | Fitting | 29.2 | 5 | 146 | Festo | Order Code: QSML-4, 10 Pc. Pack | https://www.festo.com/cat/en-us_us/products_QSM
10 | QSM-6-4 | AARL_Puppy_18_02_57_001 | Fitting | 31.6 | 3 | 94.8 | Festo | Order Code: QSM-6-4, 10 Pc. Pack | https://www.festo.com/cat/en-us_us/products_QSM
11 | QSMT-4 | AARL_Puppy_18_02_57_007 | Fitting | 38.1 | 3 | 114.3 | Festo | Order Code: QSMT-4, 10 Pc. Pack | https://www.festo.com/cat/en-us_us/products_QSM
12 | 1/4x0.75 Chicago Screw (Female) | AARL_Puppy_18_04_09_001 | Fastener | 1.81 | 52 | 94.12 | McMaster-Carr | Order Code: 99637A305, each | https://www.mcmaster.com/99637a305 | or this
13 | 1/8 ID Plastic Washer | AARL_Puppy_18_04_06_002 | Fastener | 8.24 | 1 | 8.24 | McMaster-Carr | Order Code: 90295A370, 100 Pc. Pack | https://www.mcmaster.com/90295a370
14 | 3/32 Plastic Spacer | AARL_Puppy_18_04_06_001 | Fastener | 2.29 | 1 | 2.29 | McMaster-Carr | Order Code: 90176A102, 25 Pc. Pack | https://www.mcmaster.com/90176a102
15 | 1/4 ID Roller Bearing | AARL_Puppy_18_04_03_001 | Fastener | 5.98 | 8 | 47.84 | McMaster-Carr | Order Code: 60355K503, each | https://www.mcmaster.com/60355k503 | Either this
16 | 3/16 ID Roller Bearing |  | Fastener | 6.9 | 8 | 55.2 | McMaster-Carr | Order Code: 60355K502, each | https://www.mcmaster.com/60355k502 | or this
17 | VTUG-10-MRCR-S1T-26V20-T516LA-UL-T532S-12K |  | Pneumatics | 1556.66 | 1 | 1556.66 | Festo | each | https://www.festo.com/cat/en-us_us/products_VTUG
18 | QBL-M5-5/32-U-M |  | Fitting | 31.5 | 3 | 94.5 | Festo | 10 Pc. Pack | https://www.festo.com/cat/en-us_us/products_QB
19 | QBML-5/32T-U |  | Fitting | 29.4 | 5 | 147 | Festo | 10 Pc. Pack | https://www.festo.com/cat/en-us_us/products_QB
20 | QBMT-5/32T-U |  | Fitting | 40.3 | 3 | 120.9 | Festo | 10 Pc. Pack | https://www.festo.com/cat/en-us_us/products_QB
21 | QBM-1/4T-5/32-U |  | Fitting | 31 | 3 | 93 | Festo | 10 Pc. Pack | https://www.festo.com/cat/en-us_us/products_QB
22 | 5/32 OD Tubing |  | Pneumatics | 18.3 | 1 | 18.3 | ATP | 250 ft pack | https://www.atp4pneumatics.com/product/pe04m-532bbk/
23 | MTL 5/32-U10 |  | Fitting | 0.99 | 24 | 23.76 | Mettle Air | each | https://www.mettleair.com/store/ptc/threaded-main/male-elbow/mtl-ixnpt/push-to-connect-90-elbow-fitting-5-32-od-10-32-unf-male.html
24 | MTV 5/32 |  | Fitting | 0.91 | 48 | 43.68 | Mettle Air | each | https://www.mettleair.com/store/ptc/unions-main/push-to-connect-elbow-union-5-32-od-5-32-od.html
25 | MTE 5/32-5/32 |  | Fitting | 1.33 | 24 | 31.92 | Mettle Air | each | https://www.mettleair.com/store/ptc/unions-main/mte-main/push-to-connect-tee-union-5-32-od-5-32-od.html
26 | MTU 1/4-5/32 |  | Fitting | 1.02 | 24 | 24.48 | Mettle Air | each | https://www.mettleair.com/store/ptc/unions-main/mtu-main/mtu-imp/push-to-connect-straight-union-reducer-1-4-od-5-32-od.html
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

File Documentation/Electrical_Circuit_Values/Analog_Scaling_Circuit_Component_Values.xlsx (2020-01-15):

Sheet: FA2019_FrontLeftLeg
ID | Name | Pressure Sensor |  | Potentiometer
 |  | Value | Suffix | Value | Suffix
[#] | [-] | [Ohm] | [-] | [Ohm] | [-]
1 | R1 | 3.3 | k | 33 | k
2 | R2 | 3.3 | k | 39 | k
3 | R3 | 4.7 | k | 18 | k
4 | R4 | 4.7 | k | 18 | k
5 | R5 | 3.3 | k | 39 | k
6 | R6 | 33 | k | 10 | k
7 | R7 | 3.3 | k | 33 | k
8 | R8 | 33 | k | 47 | k
9 | R9 | 4.7 | k | 18 | k
10 | R10 | 5.6 | k | 8.2 | k
11 | R11 | 4.7 | k | 18 | k
12 | R12 | 5.6 | k | 15 | k
13 | R13 | 4.7 | k | 10 | k
14 | R14 | 5.6 | k | 39 | k
15 | R15 | 4.7 | k | 12 | k
16 | R16 | 5.6 | k | 12 | k
17 | R17 | 3.3 | k | 15 | k
18 | R18 | 33 | k | 22 | k
19 | R19 | 3.3 | k | 22 | k
20 | R20 | 33 | k | 33 | k
21 | R21 | 3.3 | k | 15 | k
22 | R22 | 4.7 | k | 10 | k
23 | R23 | 4.7 | k | 12 | k
24 | R24 | 3.3 | k | 22 | k

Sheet: FA2019_BackLeftLeg
ID | Unit | Board | Channel | Front / Back | Left / Right | Joint | Muscle Type | Sensor Type | Name | Value | Suffix | Value | Quantity
[#] | [#] | [#] | [#] | [-] | [-] | [-] | [-] | [-] | [-] | [Ohm] | [-] | [Ohm] | [#]
1 | 1 | 1 | 0 | Front | Left | Hip | Ext | Pressure | R2 | 3.3 | k | 1.2 | 18
2 | 1 | 1 | 0 | Front | Left | Hip | Ext | Pressure | R3 | 4.7 | k | 1.5 | 18
3 | 1 | 1 | 0 | Front | Left | Hip | Ext | Pressure | R5 | 3.3 | k | 3.3 | 20
4 | 1 | 1 | 0 | Front | Left | Hip | Ext | Pressure | R9 | 4.7 | k | 4.7 | 12
5 | 1 | 1 | 0 | Front | Left | Hip | Ext | Pressure | R6 | 33 | k | 5.6 | 8
6 | 1 | 1 | 0 | Front | Left | Hip | Ext | Pressure | R10 | 5.6 | k | 6.8 | 2
7 | 1 | 1 | 1 | Front | Left | Hip | Flx | Pressure | R21 | 3.3 | k | 8.2 | 1
8 | 1 | 1 | 1 | Front | Left | Hip | Flx | Pressure | R22 | 4.7 | k | 10 | 4
9 | 1 | 1 | 1 | Front | Left | Hip | Flx | Pressure | R17 | 3.3 | k | 15 | 8
10 | 1 | 1 | 1 | Front | Left | Hip | Flx | Pressure | R13 | 4.7 | k | 18 | 19
11 | 1 | 1 | 1 | Front | Left | Hip | Flx | Pressure | R18 | 33 | k | 22 | 14
12 | 1 | 1 | 1 | Front | Left | Hip | Flx | Pressure | R14 | 5.6 | k | 27 | 14
13 | 1 | 1 | 2 | Front | Left | Knee | Ext | Pressure | R1 | 3.3 | k | 33 | 23
14 | 1 | 1 | 2 | Front | Left | Knee | Ext | Pressure | R4 | 4.7 | k | 39 | 5
15 | 1 | 1 | 2 | Front | Left | Knee | Ext | Pressure | R7 | 3.3 | k | 47 | 10
16 | 1 | 1 | 2 | Front | Left | Knee | Ext | Pressure | R11 | 4.7 | k | 560 | 9
17 | 1 | 1 | 2 | Front | Left | Knee | Ext | Pressure | R8 | 33 | k
18 | 1 | 1 | 2 | Front | Left | Knee | Ext | Pressure | R12 | 5.6 | k
19 | 1 | 1 | 3 | Front | Left | Knee | Flx | Pressure | R24 | 3.3 | k
20 | 1 | 1 | 3 | Front | Left | Knee | Flx | Pressure | R23 | 4.7 | k
21 | 1 | 1 | 3 | Front | Left | Knee | Flx | Pressure | R19 | 3.3 | k
22 | 1 | 1 | 3 | Front | Left | Knee | Flx | Pressure | R15 | 4.7 | k
23 | 1 | 1 | 3 | Front | Left | Knee | Flx | Pressure | R20 | 33 | k
24 | 1 | 1 | 3 | Front | Left | Knee | Flx | Pressure | R16 | 5.6 | k
25 | 1 | 2 | 0 | Front | Left | Ankle | Ext | Pressure | R2 | 3.3 | k
26 | 1 | 2 | 0 | Front | Left | Ankle | Ext | Pressure | R3 | 4.7 | k
27 | 1 | 2 | 0 | Front | Left | Ankle | Ext | Pressure | R5 | 3.3 | k
28 | 1 | 2 | 0 | Front | Left | Ankle | Ext | Pressure | R9 | 4.7 | k
29 | 1 | 2 | 0 | Front | Left | Ankle | Ext | Pressure | R6 | 33 | k
30 | 1 | 2 | 0 | Front | Left | Ankle | Ext | Pressure | R10 | 5.6 | k
31 | 1 | 2 | 1 | Front | Left | Ankle | Flx | Pressure | R21 | 3.3 | k
32 | 1 | 2 | 1 | Front | Left | Ankle | Flx | Pressure | R22 | 4.7 | k
33 | 1 | 2 | 1 | Front | Left | Ankle | Flx | Pressure | R17 | 3.3 | k
34 | 1 | 2 | 1 | Front | Left | Ankle | Flx | Pressure | R13 | 4.7 | k
35 | 1 | 2 | 1 | Front | Left | Ankle | Flx | Pressure | R18 | 33 | k
36 | 1 | 2 | 1 | Front | Left | Ankle | Flx | Pressure | R14 | 5.6 | k
37 | 1 | 3 | 0 | Front | Left | Hip |  | Potentiometer | R2 | 39 | k
38 | 1 | 3 | 0 | Front | Left | Hip |  | Potentiometer | R3 | 18 | k
39 | 1 | 3 | 0 | Front | Left | Hip |  | Potentiometer | R5 | 39 | k
40 | 1 | 3 | 0 | Front | Left | Hip |  | Potentiometer | R9 | 18 | k
41 | 1 | 3 | 0 | Front | Left | Hip |  | Potentiometer | R6 | 10 | k
42 | 1 | 3 | 0 | Front | Left | Hip |  | Potentiometer | R10 | 8.2 | k
43 | 1 | 3 | 1 | Front | Left | Knee1 |  | Potentiometer | R21 | 15 | k
44 | 1 | 3 | 1 | Front | Left | Knee1 |  | Potentiometer | R22 | 10 | k
45 | 1 | 3 | 1 | Front | Left | Knee1 |  | Potentiometer | R17 | 15 | k
46 | 1 | 3 | 1 | Front | Left | Knee1 |  | Potentiometer | R13 | 10 | k
47 | 1 | 3 | 1 | Front | Left | Knee1 |  | Potentiometer | R18 | 22 | k
48 | 1 | 3 | 1 | Front | Left | Knee1 |  | Potentiometer | R14 | 39 | k
49 | 1 | 3 | 2 | Front | Left | Knee2 |  | Potentiometer | R1 | 33 | k
50 | 1 | 3 | 2 | Front | Left | Knee2 |  | Potentiometer | R4 | 18 | k
51 | 1 | 3 | 2 | Front | Left | Knee2 |  | Potentiometer | R7 | 33 | k
52 | 1 | 3 | 2 | Front | Left | Knee2 |  | Potentiometer | R11 | 18 | k
53 | 1 | 3 | 2 | Front | Left | Knee2 |  | Potentiometer | R8 | 47 | k
54 | 1 | 3 | 2 | Front | Left | Knee2 |  | Potentiometer | R12 | 15 | k
55 | 1 | 3 | 3 | Front | Left | Ankle |  | Potentiometer | R24 | 22 | k
56 | 1 | 3 | 3 | Front | Left | Ankle |  | Potentiometer | R23 | 12 | k
57 | 1 | 3 | 3 | Front | Left | Ankle |  | Potentiometer | R19 | 22 | k
58 | 1 | 3 | 3 | Front | Left | Ankle |  | Potentiometer | R15 | 12 | k
59 | 1 | 3 | 3 | Front | Left | Ankle |  | Potentiometer | R20 | 33 | k
60 | 1 | 3 | 3 | Front | Left | Ankle |  | Potentiometer | R16 | 12 | k
61 | 2 | 4 | 0 | Back | Left | Hip | Ext | Pressure | R2 | 22 | k
62 | 2 | 4 | 0 | Back | Left | Hip | Ext | Pressure | R3 | 27 | k
63 | 2 | 4 | 0 | Back | Left | Hip | Ext | Pressure | R5 | 22 | k
64 | 2 | 4 | 0 | Back | Left | Hip | Ext | Pressure | R9 | 27 | k
65 | 2 | 4 | 0 | Back | Left | Hip | Ext | Pressure | R6 | 560
66 | 2 | 4 | 0 | Back | Left | Hip | Ext | Pressure | R10 | 33
67 | 2 | 4 | 1 | Back | Left | Hip | Flx | Pressure | R21 | 1.2 | k
68 | 2 | 4 | 1 | Back | Left | Hip | Flx | Pressure | R22 | 1.5 | k
69 | 2 | 4 | 1 | Back | Left | Hip | Flx | Pressure | R17 | 1.2 | k
70 | 2 | 4 | 1 | Back | Left | Hip | Flx | Pressure | R13 | 1.5 | k
71 | 2 | 4 | 1 | Back | Left | Hip | Flx | Pressure | R18 | 6.8 | k
72 | 2 | 4 | 1 | Back | Left | Hip | Flx | Pressure | R14 | 330
73 | 2 | 4 | 2 | Back | Left | Knee | Ext | Pressure | R1 | 22 | k
74 | 2 | 4 | 2 | Back | Left | Knee | Ext | Pressure | R4 | 27 | k
75 | 2 | 4 | 2 | Back | Left | Knee | Ext | Pressure | R7 | 22 | k
76 | 2 | 4 | 2 | Back | Left | Knee | Ext | Pressure | R11 | 27 | k
77 | 2 | 4 | 2 | Back | Left | Knee | Ext | Pressure | R8 | 560
78 | 2 | 4 | 2 | Back | Left | Knee | Ext | Pressure | R12 | 33
79 | 2 | 4 | 3 | Back | Left | Knee | Flx | Pressure | R24 | 1.2 | k
80 | 2 | 4 | 3 | Back | Left | Knee | Flx | Pressure | R23 | 1.5 | k
81 | 2 | 4 | 3 | Back | Left | Knee | Flx | Pressure | R19 | 1.2 | k
82 | 2 | 4 | 3 | Back | Left | Knee | Flx | Pressure | R15 | 1.5 | k
83 | 2 | 4 | 3 | Back | Left | Knee | Flx | Pressure | R20 | 68 | k
84 | 2 | 4 | 3 | Back | Left | Knee | Flx | Pressure | R16 | 3.3 | k
85 | 2 | 5 | 0 | Back | Left | Ankle | Ext | Pressure | R2 | 22 | k
86 | 2 | 5 | 0 | Back | Left | Ankle | Ext | Pressure | R3 | 27 | k
87 | 2 | 5 | 0 | Back | Left | Ankle | Ext | Pressure | R5 | 22 | k
88 | 2 | 5 | 0 | Back | Left | Ankle | Ext | Pressure | R9 | 27 | k
89 | 2 | 5 | 0 | Back | Left | Ankle | Ext | Pressure | R6 | 560
90 | 2 | 5 | 0 | Back | Left | Ankle | Ext | Pressure | R10 | 33
91 | 2 | 5 | 1 | Back | Left | Ankle | Flx | Pressure | R21 | 1.2 | k
92 | 2 | 5 | 1 | Back | Left | Ankle | Flx | Pressure | R22 | 1.5 | k
93 | 2 | 5 | 1 | Back | Left | Ankle | Flx | Pressure | R17 | 1.2 | k
94 | 2 | 5 | 1 | Back | Left | Ankle | Flx | Pressure | R13 | 1.5 | k
95 | 2 | 5 | 1 | Back | Left | Ankle | Flx | Pressure | R18 | 68 | k
96 | 2 | 5 | 1 | Back | Left | Ankle | Flx | Pressure | R14 | 3.3 | k
97 | 2 | 6 | 0 | Back | Left | Hip |  | Potentiometer | R2 | 18 | k
98 | 2 | 6 | 0 | Back | Left | Hip |  | Potentiometer | R3 | 12 | k
99 | 2 | 6 | 0 | Back | Left | Hip |  | Potentiometer | R5 | 18 | k
100 | 2 | 6 | 0 | Back | Left | Hip |  | Potentiometer | R9 | 12 | k
101 | 2 | 6 | 0 | Back | Left | Hip |  | Potentiometer | R6 | 5.6 | k
102 | 2 | 6 | 0 | Back | Left | Hip |  | Potentiometer | R10 | 6.8 | k
103 | 2 | 6 | 1 | Back | Left | Knee |  | Potentiometer | R21 | 18 | k
104 | 2 | 6 | 1 | Back | Left | Knee |  | Potentiometer | R22 | 12 | k
105 | 2 | 6 | 1 | Back | Left | Knee |  | Potentiometer | R17 | 18 | k
106 | 2 | 6 | 1 | Back | Left | Knee |  | Potentiometer | R13 | 12 | k
107 | 2 | 6 | 1 | Back | Left | Knee |  | Potentiometer | R18 | 33 | k
108 | 2 | 6 | 1 | Back | Left | Knee |  | Potentiometer | R14 | 47 | k
109 | 2 | 6 | 2 | Back | Left | Ankle |  | Potentiometer | R1 | 39 | k
110 | 2 | 6 | 2 | Back | Left | Ankle |  | Potentiometer | R4 | 27 | k
111 | 2 | 6 | 2 | Back | Left | Ankle |  | Potentiometer | R7 | 39 | k
112 | 2 | 6 | 2 | Back | Left | Ankle |  | Potentiometer | R11 | 27 | k
113 | 2 | 6 | 2 | Back | Left | Ankle |  | Potentiometer | R8 | 47 | k
114 | 2 | 6 | 2 | Back | Left | Ankle |  | Potentiometer | R12 | 22 | k
115 | 3 | 7 | 0 | Front | Right | Hip | Ext | Pressure | R2 | 22 | k
116 | 3 | 7 | 0 | Front | Right | Hip | Ext | Pressure | R3 | 27 | k
117 | 3 | 7 | 0 | Front | Right | Hip | Ext | Pressure | R5 | 22 | k
118 | 3 | 7 | 0 | Front | Right | Hip | Ext | Pressure | R9 | 27 | k
119 | 3 | 7 | 0 | Front | Right | Hip | Ext | Pressure | R6 | 560
120 | 3 | 7 | 0 | Front | Right | Hip | Ext | Pressure | R10 | 33
121 | 3 | 7 | 1 | Front | Right | Hip | Flx | Pressure | R21 | 1.2 | k
122 | 3 | 7 | 1 | Front | Right | Hip | Flx | Pressure | R22 | 1.5 | k
123 | 3 | 7 | 1 | Front | Right | Hip | Flx | Pressure | R17 | 1.2 | k
124 | 3 | 7 | 1 | Front | Right | Hip | Flx | Pressure | R13 | 1.5 | k
125 | 3 | 7 | 1 | Front | Right | Hip | Flx | Pressure | R18 | 68 | k
126 | 3 | 7 | 1 | Front | Right | Hip | Flx | Pressure | R14 | 3.3 | k
127 | 3 | 7 | 2 | Front | Right | Knee | Ext | Pressure | R1 | 22 | k
128 | 3 | 7 | 2 | Front | Right | Knee | Ext | Pressure | R4 | 27 | k
129 | 3 | 7 | 2 | Front | Right | Knee | Ext | Pressure | R7 | 22 | k
130 | 3 | 7 | 2 | Front | Right | Knee | Ext | Pressure | R11 | 27 | k
131 | 3 | 7 | 2 | Front | Right | Knee | Ext | Pressure | R8 | 560
132 | 3 | 7 | 2 | Front | Right | Knee | Ext | Pressure | R12 | 33
133 | 3 | 7 | 3 | Front | Right | Knee | Flx | Pressure | R24 | 1.2 | k
134 | 3 | 7 | 3 | Front | Right | Knee | Flx | Pressure | R23 | 1.5 | k
135 | 3 | 7 | 3 | Front | Right | Knee | Flx | Pressure | R19 | 1.2 | k
136 | 3 | 7 | 3 | Front | Right | Knee | Flx | Pressure | R15 | 1.5 | k
137 | 3 | 7 | 3 | Front | Right | Knee | Flx | Pressure | R20 | 68 | k
138 | 3 | 7 | 3 | Front | Right | Knee | Flx | Pressure | R16 | 3.3 | k
139 | 3 | 8 | 0 | Front | Right | Ankle | Ext | Pressure | R2 | 220 | k
140 | 3 | 8 | 0 | Front | Right | Ankle | Ext | Pressure | R3 | 270 | k
141 | 3 | 8 | 0 | Front | Right | Ankle | Ext | Pressure | R5 | 220 | k
142 | 3 | 8 | 0 | Front | Right | Ankle | Ext | Pressure | R9 | 270 | k
143 | 3 | 8 | 0 | Front | Right | Ankle | Ext | Pressure | R6 | 560
144 | 3 | 8 | 0 | Front | Right | Ankle | Ext | Pressure | R10 | 33
145 | 3 | 8 | 1 | Front | Right | Ankle | Flx | Pressure | R21 | 1.2 | k
146 | 3 | 8 | 1 | Front | Right | Ankle | Flx | Pressure | R22 | 1.5 | k
147 | 3 | 8 | 1 | Front | Right | Ankle | Flx | Pressure | R17 | 1.2 | k
148 | 3 | 8 | 1 | Front | Right | Ankle | Flx | Pressure | R13 | 1.5 | k
149 | 3 | 8 | 1 | Front | Right | Ankle | Flx | Pressure | R18 | 68 | k
150 | 3 | 8 | 1 | Front | Right | Ankle | Flx | Pressure | R14 | 3.3 | k
151 | 3 | 9 | 0 | Front | Right | Hip |  | Potentiometer | R2 | 15 | k
152 | 3 | 9 | 0 | Front | Right | Hip |  | Potentiometer | R3 | 12 | k
153 | 3 | 9 | 0 | Front | Right | Hip |  | Potentiometer | R5 | 15 | k
154 | 3 | 9 | 0 | Front | Right | Hip |  | Potentiometer | R9 | 12 | k
155 | 3 | 9 | 0 | Front | Right | Hip |  | Potentiometer | R6 | 15 | k
156 | 3 | 9 | 0 | Front | Right | Hip |  | Potentiometer | R10 | 18 | k
157 | 3 | 9 | 1 | Front | Right | Knee1 |  | Potentiometer | R21 | 18 | k
158 | 3 | 9 | 1 | Front | Right | Knee1 |  | Potentiometer | R22 | 12 | k
159 | 3 | 9 | 1 | Front | Right | Knee1 |  | Potentiometer | R17 | 18 | k
160 | 3 | 9 | 1 | Front | Right | Knee1 |  | Potentiometer | R13 | 12 | k
161 | 3 | 9 | 1 | Front | Right | Knee1 |  | Potentiometer | R18 | 47 | k
162 | 3 | 9 | 1 | Front | Right | Knee1 |  | Potentiometer | R14 | 5.6 | k
163 | 3 | 9 | 2 | Front | Right | Knee2 |  | Potentiometer | R1 | 18 | k
164 | 3 | 9 | 2 | Front | Right | Knee2 |  | Potentiometer | R4 | 12 | k
165 | 3 | 9 | 2 | Front | Right | Knee2 |  | Potentiometer | R7 | 18 | k
166 | 3 | 9 | 2 | Front | Right | Knee2 |  | Potentiometer | R11 | 12 | k
167 | 3 | 9 | 2 | Front | Right | Knee2 |  | Potentiometer | R8 | 10 | k
168 | 3 | 9 | 2 | Front | Right | Knee2 |  | Potentiometer | R12 | 15 | k
169 | 3 | 9 | 3 | Front | Right | Ankle |  | Potentiometer | R24 | 47 | k
170 | 3 | 9 | 3 | Front | Right | Ankle |  | Potentiometer | R23 | 27 | k
171 | 3 | 9 | 3 | Front | Right | Ankle |  | Potentiometer | R19 | 47 | k
172 | 3 | 9 | 3 | Front | Right | Ankle |  | Potentiometer | R15 | 27 | k
173 | 3 | 9 | 3 | Front | Right | Ankle |  | Potentiometer | R20 | 12 | k
174 | 3 | 9 | 3 | Front | Right | Ankle |  | Potentiometer | R16 | 15 | k
175 | 4 | 10 | 0 | Back | Right | Hip | Ext | Pressure | R2 | 2.2 | k
176 | 4 | 10 | 0 | Back | Right | Hip | Ext | Pressure | R3 | 2.7 | k
177 | 4 | 10 | 0 | Back | Right | Hip | Ext | Pressure | R5 | 2.2 | k
178 | 4 | 10 | 0 | Back | Right | Hip | Ext | Pressure | R9 | 2.7 | k
179 | 4 | 10 | 0 | Back | Right | Hip | Ext | Pressure | R6 | 560
180 | 4 | 10 | 0 | Back | Right | Hip | Ext | Pressure | R10 | 33
181 | 4 | 10 | 1 | Back | Right | Hip | Flx | Pressure | R21 | 1.2 | k
182 | 4 | 10 | 1 | Back | Right | Hip | Flx | Pressure | R22 | 1.5 | k
183 | 4 | 10 | 1 | Back | Right | Hip | Flx | Pressure | R17 | 1.2 | k
184 | 4 | 10 | 1 | Back | Right | Hip | Flx | Pressure | R13 | 1.5 | k
185 | 4 | 10 | 1 | Back | Right | Hip | Flx | Pressure | R18 | 68 | k
186 | 4 | 10 | 1 | Back | Right | Hip | Flx | Pressure | R14 | 3.3 | k
187 | 4 | 10 | 2 | Back | Right | Knee | Ext | Pressure | R1 | 2.2 | k
188 | 4 | 10 | 2 | Back | Right | Knee | Ext | Pressure | R4 | 2.7 | k
189 | 4 | 10 | 2 | Back | Right | Knee | Ext | Pressure | R7 | 2.2 | k
190 | 4 | 10 | 2 | Back | Right | Knee | Ext | Pressure | R11 | 2.7 | k
191 | 4 | 10 | 2 | Back | Right | Knee | Ext | Pressure | R8 | 560
192 | 4 | 10 | 2 | Back | Right | Knee | Ext | Pressure | R12 | 33
193 | 4 | 10 | 3 | Back | Right | Knee | Flx | Pressure | R24 | 1.2 | k
194 | 4 | 10 | 3 | Back | Right | Knee | Flx | Pressure | R23 | 1.5 | k
195 | 4 | 10 | 3 | Back | Right | Knee | Flx | Pressure | R19 | 1.2 | k
196 | 4 | 10 | 3 | Back | Right | Knee | Flx | Pressure | R15 | 1.5 | k
197 | 4 | 10 | 3 | Back | Right | Knee | Flx | Pressure | R20 | 68 | k
198 | 4 | 10 | 3 | Back | Right | Knee | Flx | Pressure | R16 | 3.3 | k
199 | 4 | 11 | 0 | Back | Right | Ankle | Ext | Pressure | R2 | 2.2 | k
200 | 4 | 11 | 0 | Back | Right | Ankle | Ext | Pressure | R3 | 2.7 | k
201 | 4 | 11 | 0 | Back | Right | Ankle | Ext | Pressure | R5 | 2.2 | k
202 | 4 | 11 | 0 | Back | Right | Ankle | Ext | Pressure | R9 | 2.7 | k
203 | 4 | 11 | 0 | Back | Right | Ankle | Ext | Pressure | R6 | 560
204 | 4 | 11 | 0 | Back | Right | Ankle | Ext | Pressure | R10 | 33
205 | 4 | 11 | 1 | Back | Right | Ankle | Flx | Pressure | R21 | 1.2 | k
206 | 4 | 11 | 1 | Back | Right | Ankle | Flx | Pressure | R22 | 1.5 | k
207 | 4 | 11 | 1 | Back | Right | Ankle | Flx | Pressure | R17 | 1.2 | k
208 | 4 | 11 | 1 | Back | Right | Ankle | Flx | Pressure | R13 | 1.5 | k
209 | 4 | 11 | 1 | Back | Right | Ankle | Flx | Pressure | R18 | 68 | k
210 | 4 | 11 | 1 | Back | Right | Ankle | Flx | Pressure | R14 | 3.3 | k
211 | 4 | 12 | 0 | Back | Right | Hip |  | Potentiometer | R2 | 18 | k
212 | 4 | 12 | 0 | Back | Right | Hip |  | Potentiometer | R3 | 12 | k
213 | 4 | 12 | 0 | Back | Right | Hip |  | Potentiometer | R5 | 18 | k
214 | 4 | 12 | 0 | Back | Right | Hip |  | Potentiometer | R9 | 12 | k
215 | 4 | 12 | 0 | Back | Right | Hip |  | Potentiometer | R6 | 47 | k
216 | 4 | 12 | 0 | Back | Right | Hip |  | Potentiometer | R10 | 33 | k
217 | 4 | 12 | 1 | Back | Right | Knee |  | Potentiometer | R21 | 18 | k
218 | 4 | 12 | 1 | Back | Right | Knee |  | Potentiometer | R22 | 12 | k
219 | 4 | 12 | 1 | Back | Right | Knee |  | Potentiometer | R17 | 18 | k
220 | 4 | 12 | 1 | Back | Right | Knee |  | Potentiometer | R13 | 12 | k
221 | 4 | 12 | 1 | Back | Right | Knee |  | Potentiometer | R18 | 47 | k
222 | 4 | 12 | 1 | Back | Right | Knee |  | Potentiometer | R14 | 18 | k
223 | 4 | 12 | 2 | Back | Right | Ankle |  | Potentiometer | R1 | 47 | k
224 | 4 | 12 | 2 | Back | Right | Ankle |  | Potentiometer | R4 | 33 | k
225 | 4 | 12 | 2 | Back | Right | Ankle |  | Potentiometer | R7 | 47 | k
226 | 4 | 12 | 2 | Back | Right | Ankle |  | Potentiometer | R11 | 33 | k
227 | 4 | 12 | 2 | Back | Right | Ankle |  | Potentiometer | R8 | 18 | k
228 | 4 | 12 | 2 | Back | Right | Ankle |  | Potentiometer | R12 | 33 | k

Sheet: SP2019
ID | Channel | Name | Front Left Leg
[#] | [#] | [-] | [ohm]
1 | 2 | R1 | 33.0
2 | 0 | R2 | 39.0
3 | 0 | R3 | 18.0
4 | 2 | R4 | 18.0
5 | 0 | R5 | 39.0
6 | 0 | R6 | 10.0
7 | 2 | R7 | 33.0
8 | 2 | R8 | 47.0
9 | 0 | R9 | 18.0
10 | 0 | R10 | 8.2
11 | 2 | R11 | 18.0
12 | 2 | R12 | 15.0
13 | 1 | R13 | 10.0
14 | 1 | R14 | 39.0
15 | 3 | R15 | 12.0
16 | 3 | R16 | 12.0
17 | 1 | R17 | 15.0
18 | 1 | R18 | 22.0
19 | 3 | R19 | 22.0
20 | 3 | R20 | 33.0
21 | 1 | R21 | 15.0
22 | 1 | R22 | 10.0
23 | 3 | R23 | 12.0
24 | 3 | R24 | 22.0

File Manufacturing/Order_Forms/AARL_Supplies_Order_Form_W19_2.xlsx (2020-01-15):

Item | Cost | Number | Total Cost | Vendor | Link | Notes | Order Total | 224.592
Soldering 4-Clamp Station | 39.95 | 1 | 39.95 | Amazon | https://www.amazon.com/Helping-Soldering-WorkBench-MLTOOLS-VS339/dp/B01961086E
Atmega88A-PU Microcontroller | $1.73 | 30 | $51.91 | Digikey | https://www.digikey.com/product-detail/en/microchip-technology/ATMEGA88A-PU/ATMEGA88A-PU-ND/2271010?slid=
LM324N Operational Amplifier | $0.29 | 100 | $28.93 | Digikey | https://www.digikey.com/product-detail/en/texas-instruments/LM324N/296-1391-5-ND/277627
16 MHz Crystal Oscillator | $0.95 | 25 | $23.75 | Sparkfun | https://www.sparkfun.com/products/536
2-Pin Screw Terminal, 5mm Pitch | $0.95 | 2 | $1.90 | Sparkfun | https://www.sparkfun.com/products/8432
6-Pin AVR ISP Breadboard Adapter Mini Kit | $0.95 | 25 | $23.75 | Adafruit | https://www.adafruit.com/product/1465
MCP4921-E/P 12 bit 8 pin DAC | $1.68 | 25 | $42.00 | Mouser | https://www.mouser.com/ProductDetail/Microchip-Technology/MCP4921-E-P?qs=1zyQUV6YKYz%252BhdPnOOm6sg%3D%3D
26 Pin Straight Header | $0.96 | 2 | $1.92 | Mouser | https://www.mouser.com/ProductDetail/3M-Electronic-Solutions-Division/30326-6002HB
16 Pin Straight Header | $0.79 | 1 | $0.79 | Mouser | https://www.mouser.com/ProductDetail/3M-Electronic-Solutions-Division/30316-6002HB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
6 Pin Straight Header | $0.32 | 30 | $9.69 | Mouser | https://www.mouser.com/ProductDetail/Molex/22-23-2061

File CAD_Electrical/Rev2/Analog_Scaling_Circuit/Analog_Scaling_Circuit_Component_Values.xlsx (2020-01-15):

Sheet: FA2019_FrontLeftLeg
ID | Name | Pressure Sensor |  | Potentiometer
 |  | Value | Suffix | Value | Suffix
[#] | [-] | [Ohm] | [-] | [Ohm] | [-]
1 | R1 | 3.3 | k | 33 | k
2 | R2 | 3.3 | k | 39 | k
3 | R3 | 4.7 | k | 18 | k
4 | R4 | 4.7 | k | 18 | k
5 | R5 | 3.3 | k | 39 | k
6 | R6 | 33 | k | 10 | k
7 | R7 | 3.3 | k | 33 | k
8 | R8 | 33 | k | 47 | k
9 | R9 | 4.7 | k | 18 | k
10 | R10 | 5.6 | k | 8.2 | k
11 | R11 | 4.7 | k | 18 | k
12 | R12 | 5.6 | k | 15 | k
13 | R13 | 4.7 | k | 10 | k
14 | R14 | 5.6 | k | 39 | k
15 | R15 | 4.7 | k | 12 | k
16 | R16 | 5.6 | k | 12 | k
17 | R17 | 3.3 | k | 15 | k
18 | R18 | 33 | k | 22 | k
19 | R19 | 3.3 | k | 22 | k
20 | R20 | 33 | k | 33 | k
21 | R21 | 3.3 | k | 15 | k
22 | R22 | 4.7 | k | 10 | k
23 | R23 | 4.7 | k | 12 | k
24 | R24 | 3.3 | k | 22 | k
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

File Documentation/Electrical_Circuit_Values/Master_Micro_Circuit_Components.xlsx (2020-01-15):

ID | Part | Value | Modifier
[#] | [-] | [O/F] | [-]
1 | R1 | 10.00 | k
2 | R4 | 82.00 | k
3 | R5 | 330.00 | k
4 | C1 | 22.00 | p
5 | C2 | 22.00 | p
6 | C3 | 0.10 | mu
7 | C4 | 0.10 | mu
8 | C5 | 0.10 | mu

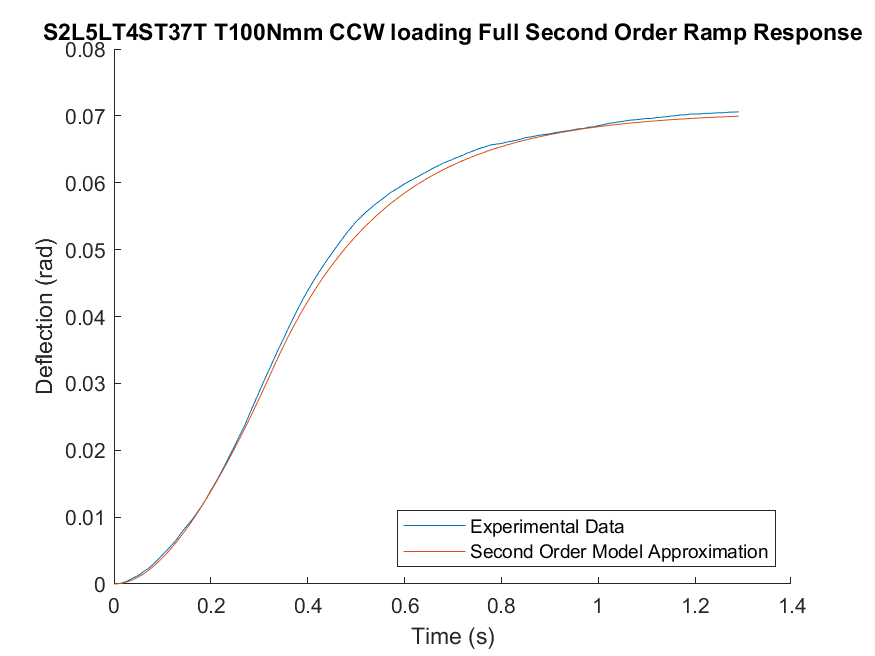
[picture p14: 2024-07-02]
Code/Matlab/Analysis/DampedLeg_Zheng/3DPrinted_Torsion_Spring/torqueTest/Figures/FirstOrder/S2L5LT4ST37T T100Nmm CCW loading Full Second Order Ramp Response.png

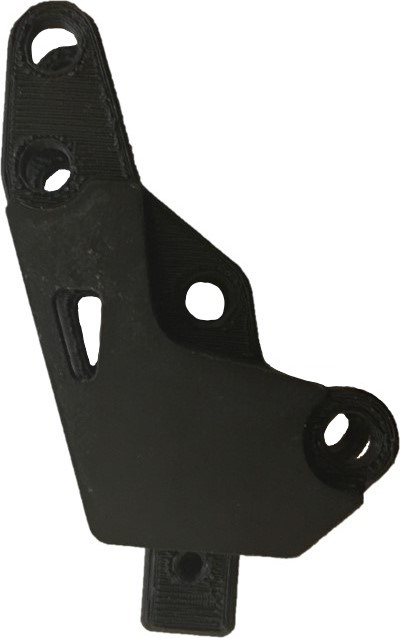
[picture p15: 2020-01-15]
Documentation/Pictures/PSU_Puppy_Pictures/Lower_Knee2_Component.jpg

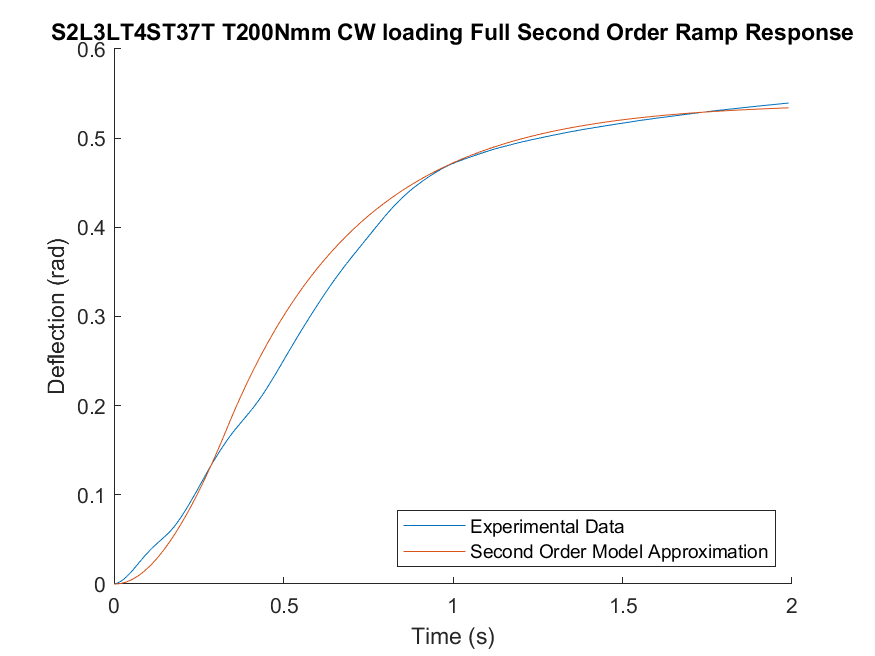
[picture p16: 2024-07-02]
Code/Matlab/Analysis/DampedLeg_Zheng/3DPrinted_Torsion_Spring/torqueTest/Figures/FirstOrder/S2L3LT4ST37T T200Nmm CW loading Full Second Order Ramp Response.png

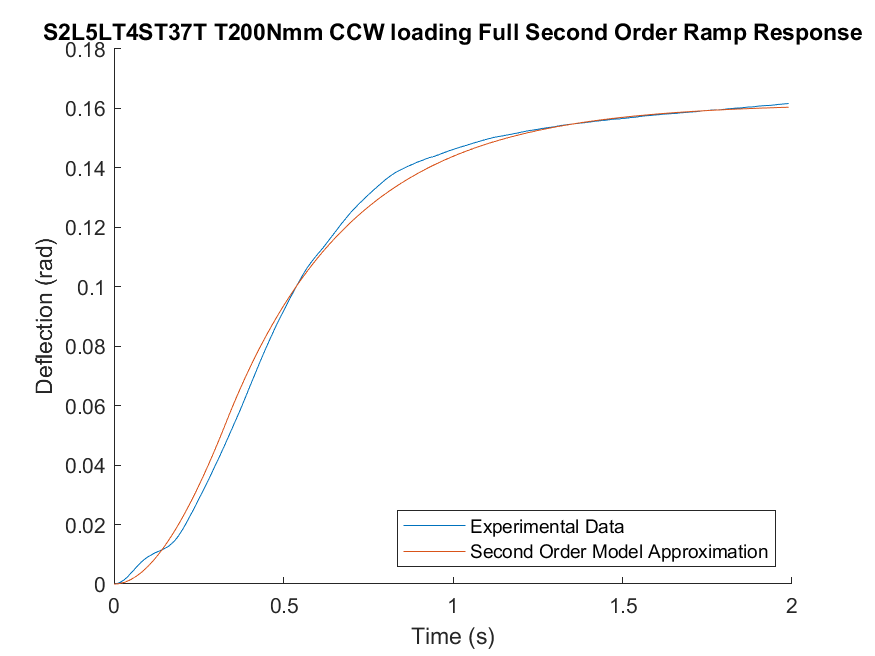
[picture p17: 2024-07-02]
Code/Matlab/Analysis/DampedLeg_Zheng/3DPrinted_Torsion_Spring/torqueTest/Figures/FirstOrder/S2L5LT4ST37T T200Nmm CCW loading Full Second Order Ramp Response.png

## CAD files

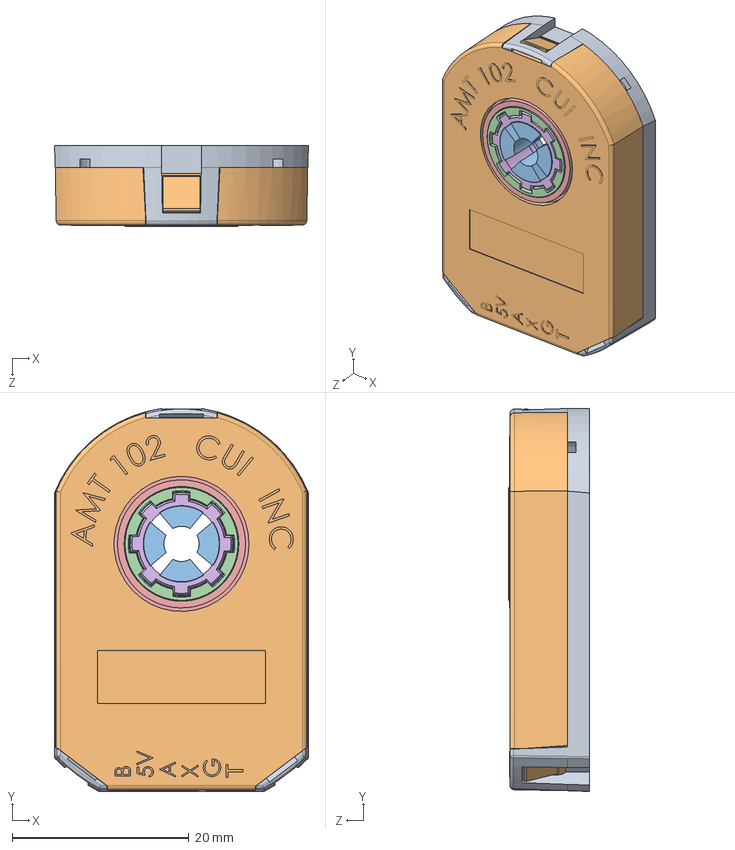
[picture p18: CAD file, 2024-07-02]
CAD_Mechanical/AARL_QR-Quadruped/AARL_QR_EL-Electronics/AARL_QR_EL_EN1-Encoder1/AARL_QR_EL_EN1-amt102-0048-i4000-s.sldasm
28.8 x 43.4 x 9.15 mm
AARL_QR_EL_EN1_001-CUI_DEVICES_amt-102-base-rev-k
AARL_QR_EL_EN1_002-CUI_DEVICES_amt-102-top-cover-rev-h
AARL_QR_EL_EN1_003-CUI_DEVICES_amt-sleeve-rev-d(4mm)
AARL_QR_EL_EN1_004-CUI_DEVICES_amt-hub-top-rev-d1
AARL_QR_EL_EN1_005-CUI_DEVICES_amt-hub-bottom-rev-b
AARL_QR_EL_EN1_006-CUI_DEVICES_amt10x-shaft-adaptor-rev-e
AARL_QR_EL_EN1_007-CUI_DEVICES_receiver-board
AARL_QR_EL_EN1_008-CUI_DEVICES_rotor-board-rev f
AARL_QR_EL_EN1_009-CUI_DEVICES_transmitter-board amt10(amt-102)

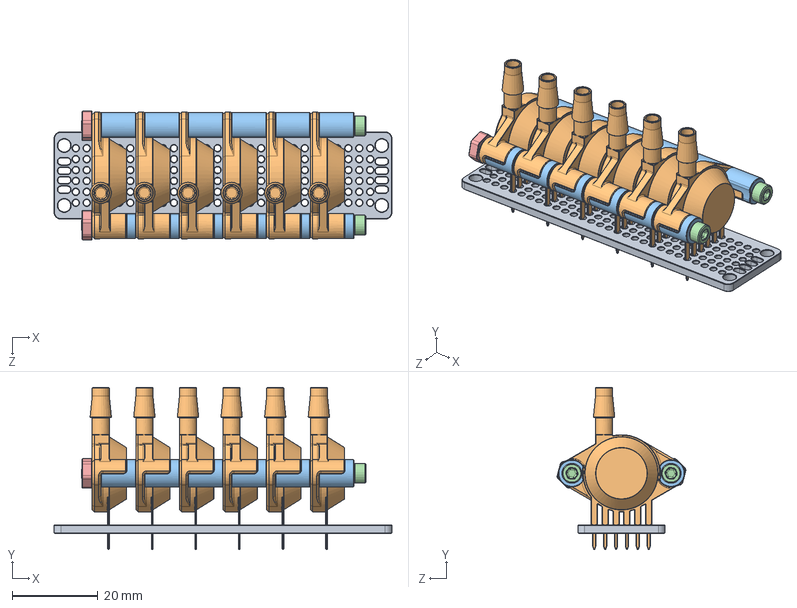
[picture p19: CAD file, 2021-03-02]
CAD_Mechanical/AARL_QR-Quadruped/AARL_QR_EL-Electronics/AARL_QR_EL_PA-Pressure_Sensor_Array/AARL_QR_EL_PA_000-Pressure_Sensor_Array.SLDASM
78.7 x 37.8 x 30.0 mm
AARL_Puppy_18_03_01_009
AARL_Puppy_18_03_01_002-MPX5700GP x 6
AARL_Puppy_18_03_01_010 x 12
AARL_Puppy_18_04_01_014 x 2
AARL_QR_HW_NU_002 x 2

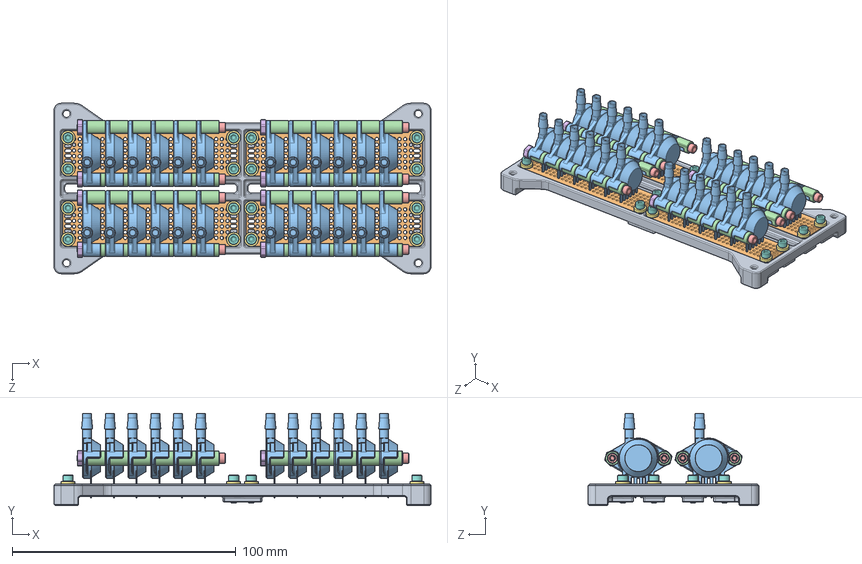
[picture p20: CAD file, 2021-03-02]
CAD_Mechanical/AARL_QR-Quadruped/AARL_QR_EL-Electronics/AARL_QR_EL_PM-Pressure_Sensor_Mounting/AARL_QR_EL_PM-Pressure_Sensor_Mounting.SLDASM
168.4 x 41.1 x 76.2 mm
AARL_QR_EL_PM_014
AARL_Puppy_18_03_01_009 x 4
AARL_Puppy_18_03_01_002-MPX5700GP x 24
AARL_Puppy_18_03_01_010 x 48
AARL_Puppy_18_04_01_014 x 8
AARL_QR_HW_NU_002 x 24
AARL_QR_HW_WA_002 x 16
AARL_QR_HW_CS_033-4-40x0375 x 16

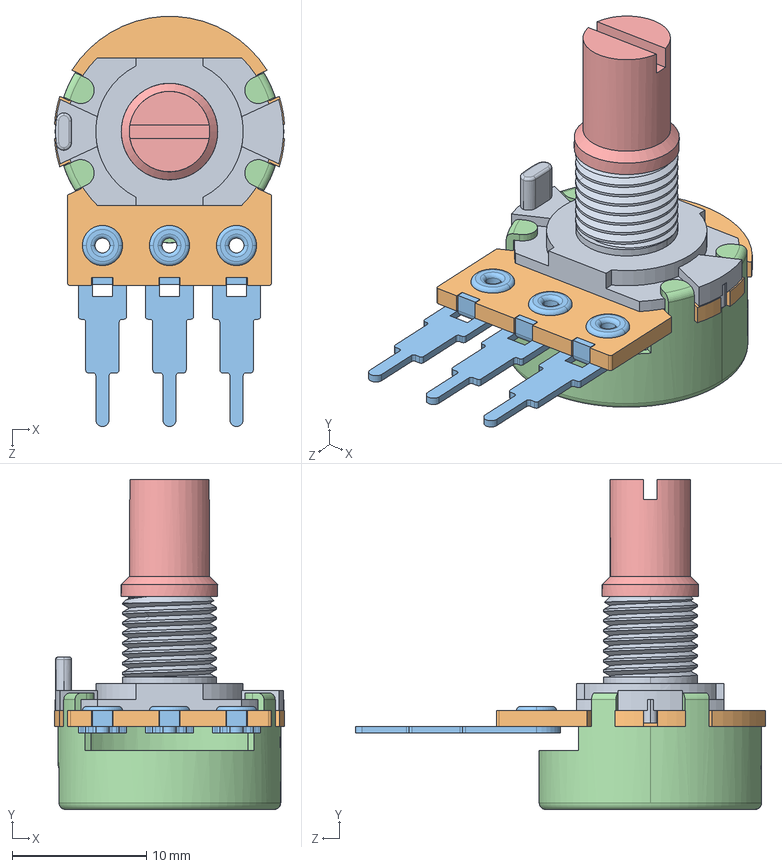
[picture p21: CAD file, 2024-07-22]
CAD_Mechanical/AARL_QR-Quadruped/AARL_QR_EL-Electronics/AARL_QR_EL_PT-Potentiometers/AARL_QR_EL_PT_000-P160KN26L.SLDASM
17.2 x 24.6 x 30.6 mm
AARL_QR_EL_PT_001
AARL_QR_EL_PT_002
AARL_QR_EL_PT_003 x 3
AARL_QR_EL_PT_004
AARL_QR_EL_PT_005

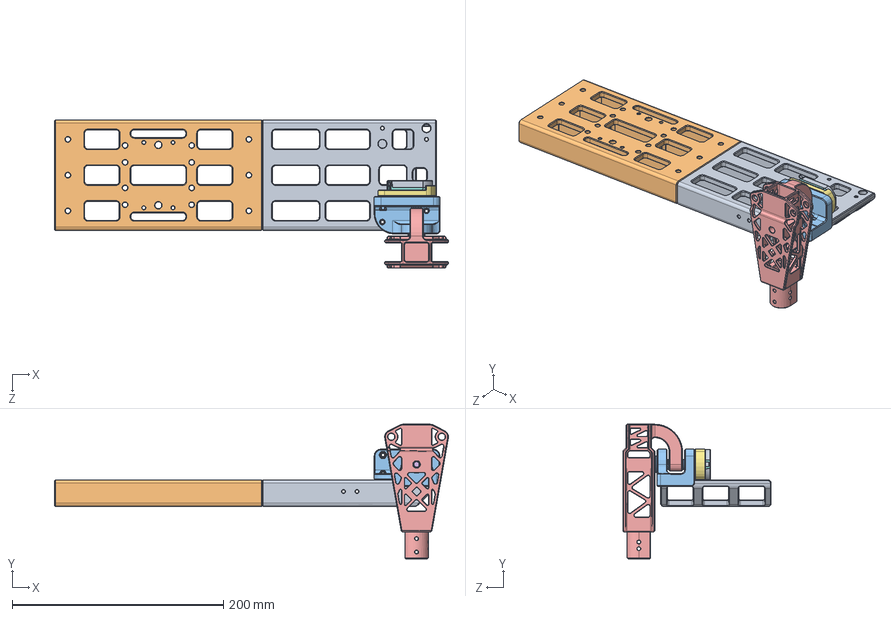
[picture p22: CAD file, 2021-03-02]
CAD_Mechanical/AARL_QR-Quadruped/AARL_QR_FR-Frame/AARL_QR_FR_BO-Body/InProgress/Jasmin/AARL_Puppy_18_01_01_007.SLDASM
373.3 x 127.5 x 140.6 mm
AARL_Puppy_18_01_01_057
AARL_Puppy_18_01_01_059
AARL_Puppy_18_01_01_060_R
AARL_Puppy_18_04_03_004 x 2
AARL_Puppy_18_01_02_053
AARL_QR_HW_ST_001-8632T132_D_PROFILE_SHAFT_LONG
AARL_Puppy_18_01_04_043
AARL_QR_EL_EN2_001-CUI_DEVICES_amt-102-base-rev-k
AARL_QR_EL_EN2_002-CUI_DEVICES_amt-102-top-cover-rev-h
AARL_QR_EL_EN2_003-CUI_DEVICES_amt-sleeve-rev-d(d)
AARL_QR_EL_EN2_004-CUI_DEVICES_amt-hub-top-rev-d1
AARL_QR_EL_EN2_005-CUI_DEVICES_amt-hub-bottom-rev-b
AARL_QR_EL_EN2_006-CUI_DEVICES_amt10x-shaft-adaptor-rev-e
AARL_QR_EL_EN2_007-CUI_DEVICES_receiver-board
AARL_QR_EL_EN2_008-CUI_DEVICES_rotor-board-rev f
AARL_QR_EL_EN2_009-CUI_DEVICES_transmitter-board amt10(amt-102)

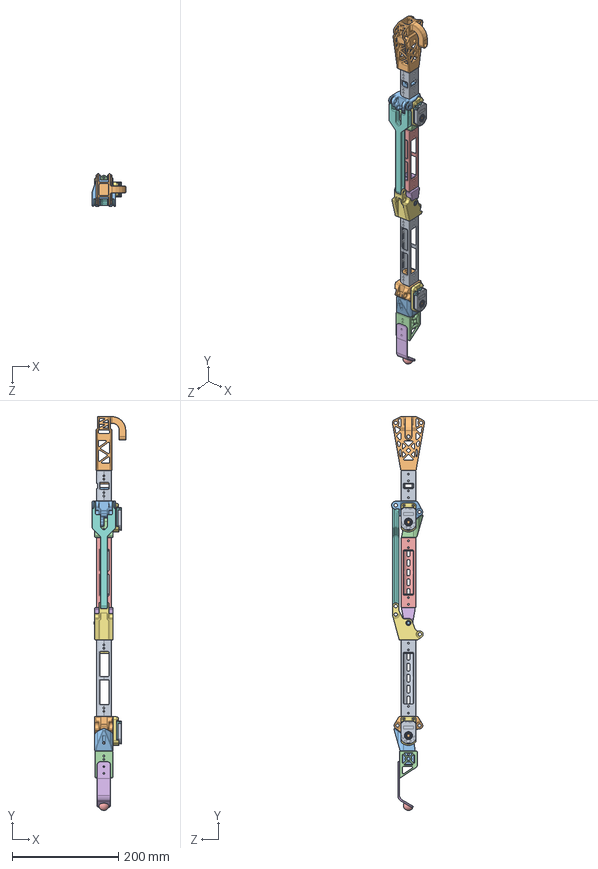
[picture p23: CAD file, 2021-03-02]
CAD_Mechanical/AARL_QR-Quadruped/AARL_QR_FR-Frame/AARL_QR_FR_LE-Legs/AARL_QR_FR_LE_PA-Pantograph/AARL_QR_FR_LE_PA_FL-Front_Left/InProgress/Jasmin/AARL_Puppy_18_01_06_002.SLDASM
63.7 x 741.9 x 62.0 mm
AARL_Puppy_18_01_06_39
AARL_Puppy_18_01_02_053
AARL_Puppy_18_01_06_042
AARL_Puppy_18_01_04_039_R
AARL_Puppy_18_01_06_40
AARL_Puppy_18_01_06_036_L
AARL_Puppy_18_01_06_38
AARL_Puppy_18_01_06_037
AARL_Puppy_18_01_06_41
AARL_Puppy_18_01_04_040
AARL_Puppy_18_01_04_039_L
AARL_Puppy_18_01_04_041
AARL_Puppy_18_01_02_022
AARL_Puppy_18_01_02_017
AARL_Puppy_18_01_04_043 x 2
AARL_QR_EL_EN2_001-CUI_DEVICES_amt-102-base-rev-k x 2
AARL_QR_EL_EN2_002-CUI_DEVICES_amt-102-top-cover-rev-h x 2
AARL_QR_EL_EN2_003-CUI_DEVICES_amt-sleeve-rev-d(d) x 2
AARL_QR_EL_EN2_004-CUI_DEVICES_amt-hub-top-rev-d1 x 2
AARL_QR_EL_EN2_005-CUI_DEVICES_amt-hub-bottom-rev-b x 2
AARL_QR_EL_EN2_006-CUI_DEVICES_amt10x-shaft-adaptor-rev-e x 2
AARL_QR_EL_EN2_007-CUI_DEVICES_receiver-board x 2
AARL_QR_EL_EN2_008-CUI_DEVICES_rotor-board-rev f x 2
AARL_QR_EL_EN2_009-CUI_DEVICES_transmitter-board amt10(amt-102) x 2
AARL_QR_HW_BE_004-6377K310_ULTRA-LOW-FRICTION DRY-RUNNING SLEEVE BEARING x 6
AARL_QR_HW_ST_002-8632T132_D_PROFILE_SHAFT_SHORT x 2
AARL_QR_HW_ST_002-8632T132_D_PROFILE_SHAFT_SHORTER

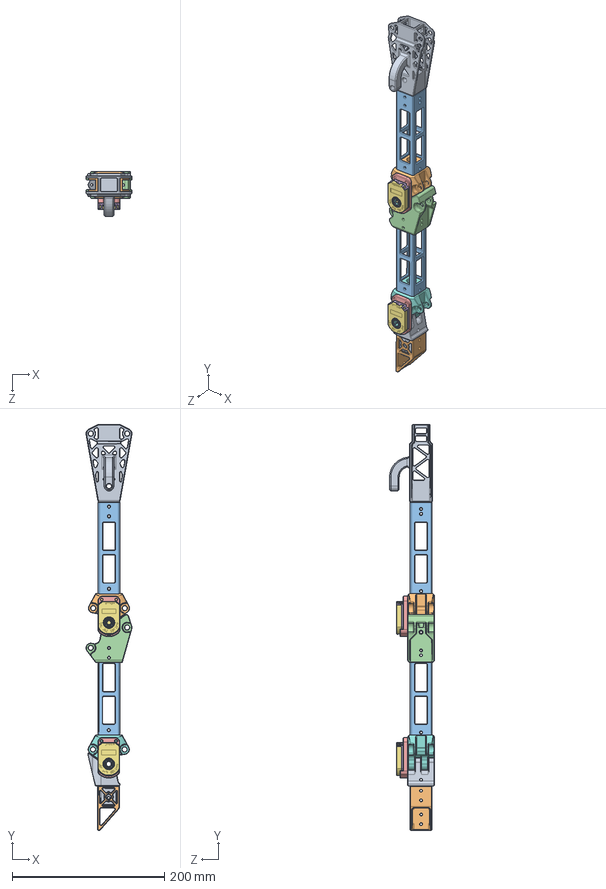
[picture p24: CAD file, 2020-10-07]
CAD_Mechanical/AARL_QR-Quadruped/AARL_QR_FR-Frame/AARL_QR_FR_LE-Legs/AARL_QR_FR_LE_PL-Plain/AARL_QR_FR_LE_PL_BR-Back_Right/InProgress/Jasmin/AARL_Puppy_18_01_05_001.SLDASM
60.5 x 533.5 x 59.0 mm
AARL_Puppy_18_01_02_051
AARL_Puppy_18_01_04_027
AARL_Puppy_18_01_04_024 x 2
AARL_Puppy_18_01_04_30
AARL_Puppy_18_01_04_022 x 2
AARL_QR_EL_EN2_001-CUI_DEVICES_amt-102-base-rev-k x 2
AARL_QR_EL_EN2_002-CUI_DEVICES_amt-102-top-cover-rev-h x 2
AARL_QR_EL_EN2_003-CUI_DEVICES_amt-sleeve-rev-d(d) x 2
AARL_QR_EL_EN2_004-CUI_DEVICES_amt-hub-top-rev-d1 x 2
AARL_QR_EL_EN2_005-CUI_DEVICES_amt-hub-bottom-rev-b x 2
AARL_QR_EL_EN2_006-CUI_DEVICES_amt10x-shaft-adaptor-rev-e x 2
AARL_QR_EL_EN2_007-CUI_DEVICES_receiver-board x 2
AARL_QR_EL_EN2_008-CUI_DEVICES_rotor-board-rev f x 2
AARL_QR_EL_EN2_009-CUI_DEVICES_transmitter-board amt10(amt-102) x 2
AARL_Puppy_18_01_04_029
AARL_Puppy_18_01_04_32
AARL_Puppy_18_01_04_033
AARL_Puppy_18_01_04_034

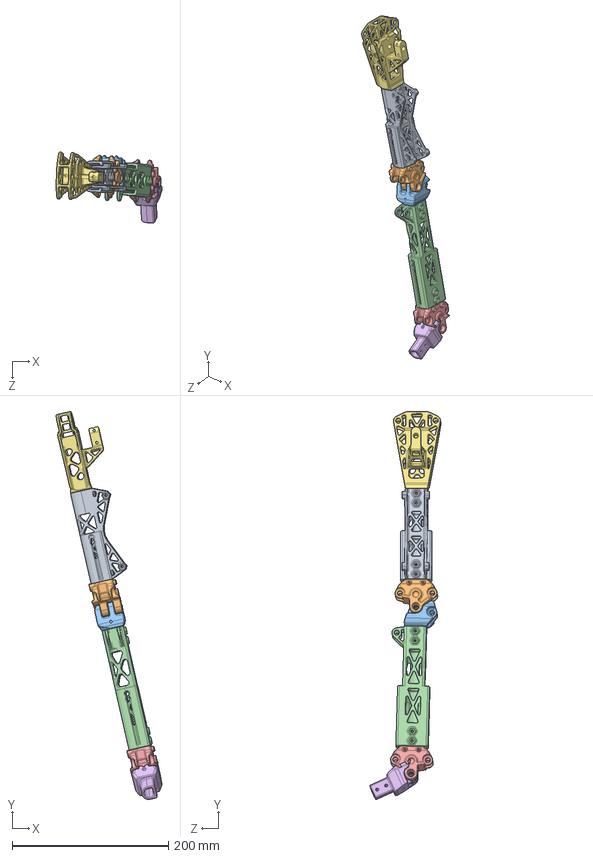
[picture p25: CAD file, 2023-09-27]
CAD_Mechanical/AARL_QR-Quadruped/AARL_QR_FR-Frame/InProgress/Manuel/AARL_QR_FR_Manuel_Mansilla/AARL_QR_FR_Manuel_Mansilla/left back leg/left back leg.SLDASM
135.8 x 497.0 x 91.0 mm
AARL_QR_FR_LE_PL_BL_002.2
AARL_QR_FR_LE_PL_BL_003.1
AARL_QR_FR_LE_PL_BL_004.1.1
AARL_QR_FR_LE_PL_BL_005.1
AARL_QR_FR_LE_PL_BL_006.1
AARL_QR_FR_LE_PL_BL_007.1
AARL_QR_FR_LE_PL_BL_012.1

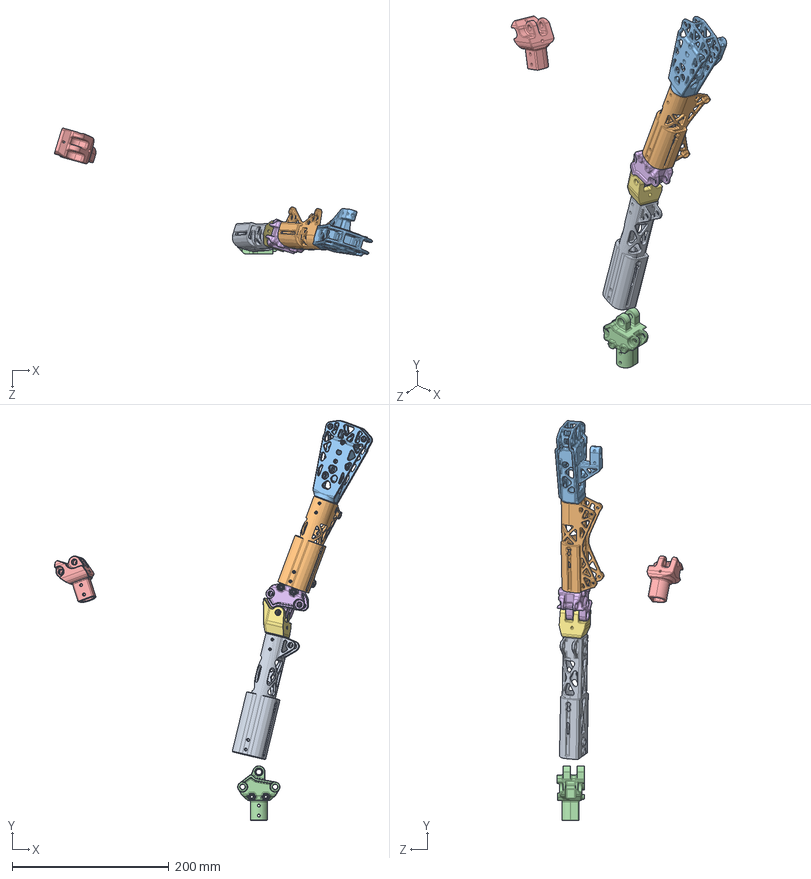
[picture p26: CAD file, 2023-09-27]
CAD_Mechanical/AARL_QR-Quadruped/AARL_QR_FR-Frame/InProgress/Manuel/AARL_QR_FR_Manuel_Mansilla/AARL_QR_FR_Manuel_Mansilla/Right back leg/right back leg.SLDASM
406.2 x 510.5 x 163.5 mm
AARL_QR_FR_LE_PL_BL_005.1
AARL_QR_FR_LE_PL_BL_002.2
AARL_QR_FR_LE_PL_BL_012.1
AARL_QR_FR_LE_PL_BR_003.10
AARL_QR_FR_LE_PL_BR_004.10
AARL_QR_FR_LE_PL_BR_006.10
AARL_QR_FR_LE_PL_BR_007.10

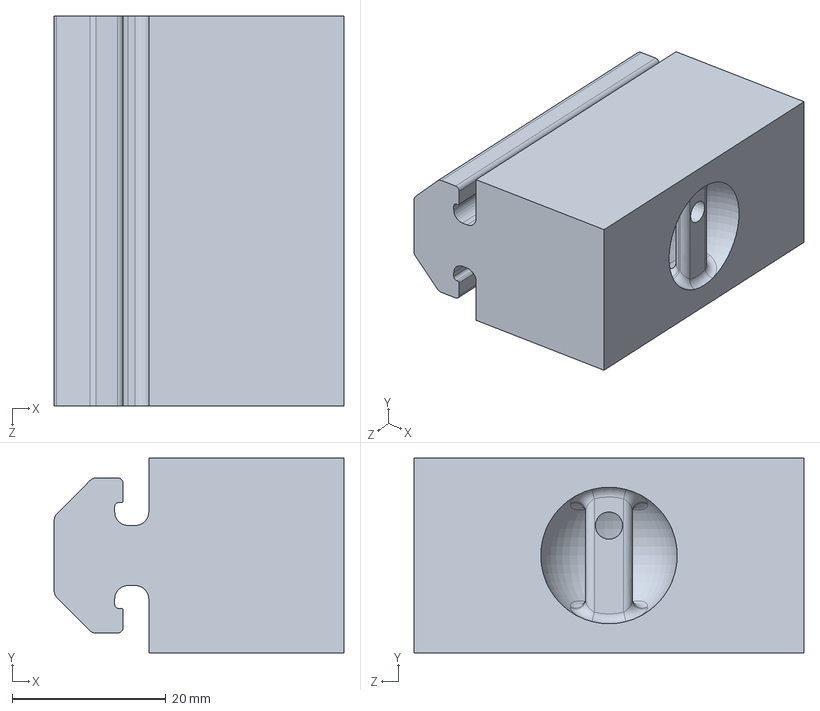
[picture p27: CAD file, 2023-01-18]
CAD_Mechanical/AARL_QR-Quadruped/AARL_QR_FR-Frame/InProgress/Sabrina/TslotAttachmentAssem.SLDASM
37.7 x 25.4 x 50.8 mm

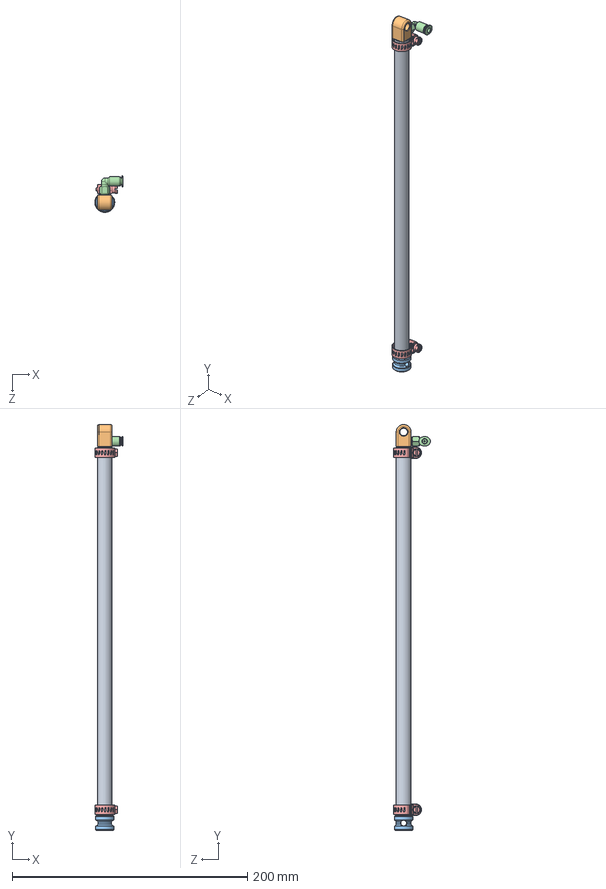
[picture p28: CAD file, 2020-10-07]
CAD_Mechanical/AARL_QR-Quadruped/AARL_QR_PN-Pneumatics/AARL_QR_PN_BLFE-BLFE/AARL_QR_PN_BLFE_000-BLFE.SLDASM
24.2 x 345.3 x 31.3 mm
AARL_Puppy_18_02_45_001
AARL_Puppy_18_02_01_010
AARL_Puppy_18_02_01_011
AARL_Puppy_18_02_57_010-QSML-M3-4
AARL_Puppy_18_02_57_011-5388K140_Hose-Clamp x 2

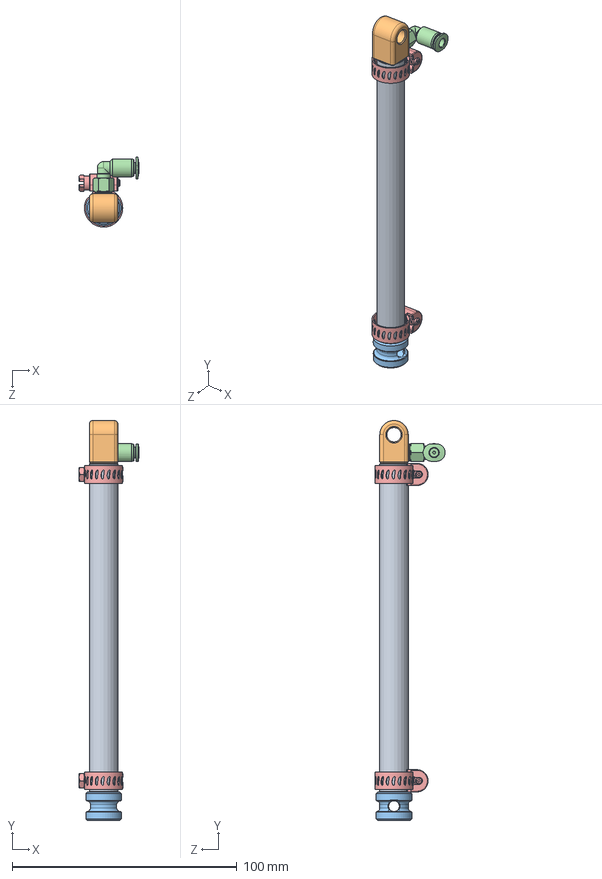
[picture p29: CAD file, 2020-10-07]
CAD_Mechanical/AARL_QR-Quadruped/AARL_QR_PN-Pneumatics/AARL_QR_PN_BLMF-BLMF/AARL_QR_PN_BLTF_000-BLTF.SLDASM
26.6 x 178.0 x 31.3 mm
AARL_Puppy_18_02_50_001
AARL_Puppy_18_02_01_010
AARL_Puppy_18_02_01_011
AARL_Puppy_18_02_57_010-QSML-M3-4
AARL_Puppy_18_02_57_011-5388K140_Hose-Clamp x 2

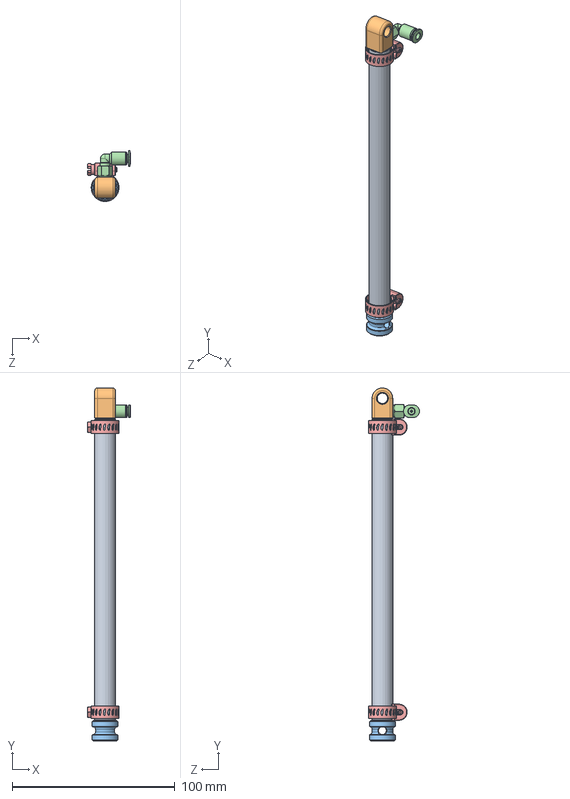
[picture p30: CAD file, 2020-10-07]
CAD_Mechanical/AARL_QR-Quadruped/AARL_QR_PN-Pneumatics/AARL_QR_PN_BLTE-BLTE/AARL_QR_PN_BLME_000-BLME.SLDASM
26.6 x 216.7 x 31.3 mm
AARL_Puppy_18_02_47_001
AARL_Puppy_18_02_01_010
AARL_Puppy_18_02_01_011
AARL_Puppy_18_02_57_010-QSML-M3-4
AARL_Puppy_18_02_57_011-5388K140_Hose-Clamp x 2

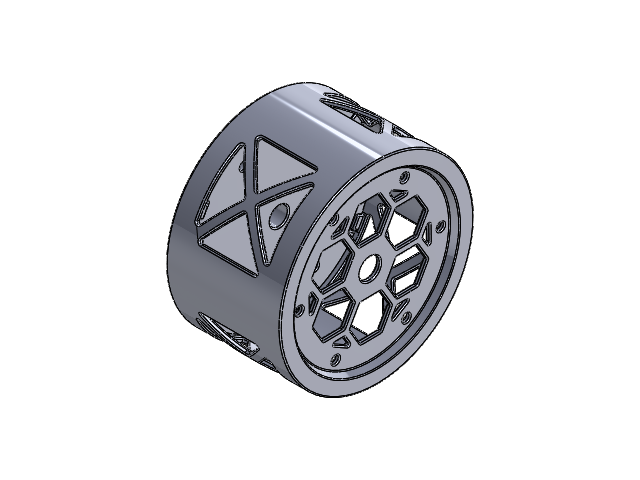
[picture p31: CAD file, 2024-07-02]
CAD_Mechanical/AARL_QR-Quadruped/AARL_QR_FR-Frame/InProgress/Haonan/AARL_QR_FR_LE_BI_BL-Back_Left_new/Adjustable Spiral Torsion Spring/Adjustable Spring Assembly v3.SLDASM
Housing Body Cap v4
Housing Body v4

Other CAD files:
CAD_Mechanical/AARL_QR-Quadruped/AARL_QR_EL-Electronics/AARL_QR_EL_EN2-Encoder2/AARL_QR_EL_EN2-amt102-0048-i6350-s.sldasm
CAD_Mechanical/AARL_QR-Quadruped/AARL_QR_FR-Frame/InProgress/Haonan/AARL_QR_FR_LE_BI_BL-Back_Left_new/Adjustable Spiral Torsion Spring/Spring/Dynamixel_Test_Stand/Test_Stand_Assembly.SLDASM
CAD_Mechanical/AARL_QR-Quadruped/AARL_QR_PN-Pneumatics/AARL_QR_PN_BLTF-BLTF/AARL_QR_PN_BLMF_000-BLMF.SLDASM
CAD_Mechanical/AARL_QR-Quadruped/AARL_QR_PN-Pneumatics/AARL_QR_PN_BRFE-BRFE/AARL_QR_PN_BRFE_000-BRFE.SLDASM
CAD_Mechanical/AARL_QR-Quadruped/AARL_QR_BA-Biarticular/Complete/6389K352_LIGHT DUTY DRY-RUNNING SLEEVE BEARING.SLDPRT
CAD_Mechanical/AARL_QR-Quadruped/AARL_QR_BA-Biarticular/Complete/91251A191_BLACK-OXIDE ALLOY STEEL SOCKET HEAD CAP SCREW (1).SLDPRT
CAD_Mechanical/AARL_QR-Quadruped/AARL_QR_BA-Biarticular/Complete/93365A110_HEAT-SET INSERTS FOR PLASTICS.SLDPRT
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

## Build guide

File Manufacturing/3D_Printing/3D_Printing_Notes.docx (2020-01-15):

3D Printer Setting Options

Fill Pattern

- Honey Comb & Triangular infills are the strongest infill patterns.
- Honey Comb infills have more uniform in-plane material properties than triangle infills, which tend to be strongest along the walls of the triangle.
- Our 3D printer recommends triangular infill for its pathing algorithm for speed and strength.
- Rectangular infill is generally the quickest infill pattern to print, but again our printer recommends using triangular infill for speed based on its algorithm.

Fill Density

- Increasing infill density improves component strength, but suffers from diminishing returns.
- Increasing from 75% to 100% infill density will increase the strength significantly less than an increase from 25% to 50% infill density.

Wall & Ceiling/Floor Layers

- Increasing the number of shell layers will improve the durability of a tapped holes.
- Increasing the number of shell layers also provides more viable material for post processing (eg, sanding).
- Increasing the number of shell layers can improve the wear characteristics of the part. Ie, by increasing the amount of material that would need to wear down before a critical failure occurs.

Layer Height

- Decreasing layer height improves the surface finish of the part.
- Increasing layer height improves the strength of a part. This is because the weakest locations on a 3D printed part are between the layers. The area between layers also tends to act as a stress concentration. It only take one defective layer for the part to have significantly reduced strength and stiffness characteristics.
- Increasing layer height provides more material for post processing in the z-direction.

Fiber

- See the material properties datasheet for a comparison of the fibers we have available.
- Adding fiber significantly improves the strength and stiffness of the part (>15x stronger and stiffer).
- Adding fiber around tapped holes significantly improves the quality of those holes.
- Adding fiber around the outside of a part makes the part more wear resistant.

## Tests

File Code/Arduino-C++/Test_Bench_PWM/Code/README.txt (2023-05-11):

1. dtOff_Test:
This program demonstrates a method that 
adjusts duty cycle by changing the amount of
time the signal is on LOW per period. The
amount of time the signal is on HIGH per
period is kept constant. Time on HIGH and
active muscle can be edited in the code.

2. dtOn_Test:
This program demonstrates a method that 
adjusts duty cycle by changing the amount of
time the signal is on HIGH per period. 
Frequency/period are kept constant. 
The program increments amount of time on HIGH
by 1 millisecond every 10 seconds. Frequency
and active muscle can be edited in the code.

3. Read_Pressure_Sensors:
This program outputs pressure readings 
(converted to kPA) when pulsing the active
muscle at a user-specified duty cycle
(entered into serial monitor). Active muscle
can be edited in the code.

4. Step_Demo:
This program produces a "stepping" motion in
the test bench leg when run. Target angle
constants, stage length constants, and the
statements within each stage's if block can
be edited to customize the motion sequence. 
(See comments in program for more details.)

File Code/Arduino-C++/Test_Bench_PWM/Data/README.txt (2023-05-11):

1. Duty_Cycle_vs_Joint_Angle:
Data was collected at a constant frequency of
20 Hz in 1 second intervals. See dtOn_Test in
Test_Bench_PWM/Code for data collection
program.

2. Equation_Sheet:
Best fit equations for data in
Duty_Cycle_vs_Joint_Angle.

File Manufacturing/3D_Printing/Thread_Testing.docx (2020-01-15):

Overview

- What printer settings should be used to improve tapping viability?
  - Use fiber in concentric rings around the holes to be tapped.
  - Increase the number of wall layers around the holes to be tapped.
  - Increase the fill density of the part. Should use at least the default fill density value (37%).
  - Increase the number of roof & floor layers.
- What printer settings do not have a significant impact on tapping viability?
  - Layer height
  - Layer direction
  - Infill pattern
- In order, which settings are most important to improving tapping viability?
  1. Fiber,
  2. Number of wall layers,
  3. Fill density,
  4. Roof & floor layers,
  5. Layer height,
  6. Layer direction,
  7. Infill pattern.

Printer Setting vs Tapping Viability Details

- How does layer direction affect tapping viability?
  - The layer direction does not appear to have a significant effect on thread strength.
  - Since layer direction clearly does generally affect the strength of the part under most loading conditions, it is possible that further testing would reveal a more significant difference in strength when threading with or against the layer direction. However, preliminary testing reveals this effect to be minimal.
  - Since layer direction appears to have little affect on the viability of tapping and tapped holes can occur along many axes within a part, I recommend that layer direction is chosen to satisfy other design or printing requirements, instead of specifically for tapping considerations.
- How does fill density affect tapping viability?
  - Fill density affects tapping viability primarily in that it strengthens the region of the part surrounding the threaded hole, rather than strengthening the threads themselves.
  - For example, the default fill settings with a triangular fill pattern were sufficient to prevent fasteners from being pulled out axially. Increasing the fill density beyond this point did not significantly improve axial strength. However, increasing the fill density to its maximum value (57%) , or even using solid fill, did improve the strength of the threads with respect to radial loading on the fastener.
  - To prevent fittings/fasteners from pulling out, I recommend using at least the default fill density setting. If the fastener will experience primarily radial loading, I recommend increasing the fill density as much as possible to prevent pulling out and strengthen the nearby material.
- How does fill pattern affect tapping viability?
  - Fill pattern has no significant effect on tapping viability.
  - Rectangular fill yielded a slight improvement, but this is likely due to the inherent increase in fill density when using rectangular fill compared to other fill patterns.
  - I recommend choosing infill pattern based on other design considerations, and not tapping viability.
- How does layer height affect tapping viability?
  - The larger layer height test case caused the face of the part to rip off before pulling out the threads. This indicates that layer height may improve tapping viability.
  - Aside from this one test case, there was little relationship between the layer height and tapping viability.
  - I recommend using the largest layer height possible if surface finish or fit requirements do not necessitate a smaller layer height.
- How does the number of roof & floor layers affect tapping viability?
  - Roof & floor layers may slightly improve tapping viability, but this improvement is small.
  - I recommend increasing the root and floor layers to improve tapping viability. However, altering this property alone will likely not improve the results significantly.
- How does the number of wall layers affect tapping viability?
  - Increasing the quantity of wall layers significantly improves tapping viability.
  - The improvement here is second only to the addition of fiber about the holes.
  - The part may still suffer from weakness in the region beyond the wall layers.
- How does fiber affect tapping viability?
  - The addition of two concentric rings of carbon fiber around the thread holes significantly improved threading viability.
  - In this case, the material surrounding the hole broke before the threads pulled out, even under radial loads.
  - While other fibers have not yet been tested, they likely result in similar improvements.
  - I recommend using fiber around threaded holes when the other suggestions listed herein are insufficient to prevent threads from pulling through.

Tapping Viability vs Printer Settings

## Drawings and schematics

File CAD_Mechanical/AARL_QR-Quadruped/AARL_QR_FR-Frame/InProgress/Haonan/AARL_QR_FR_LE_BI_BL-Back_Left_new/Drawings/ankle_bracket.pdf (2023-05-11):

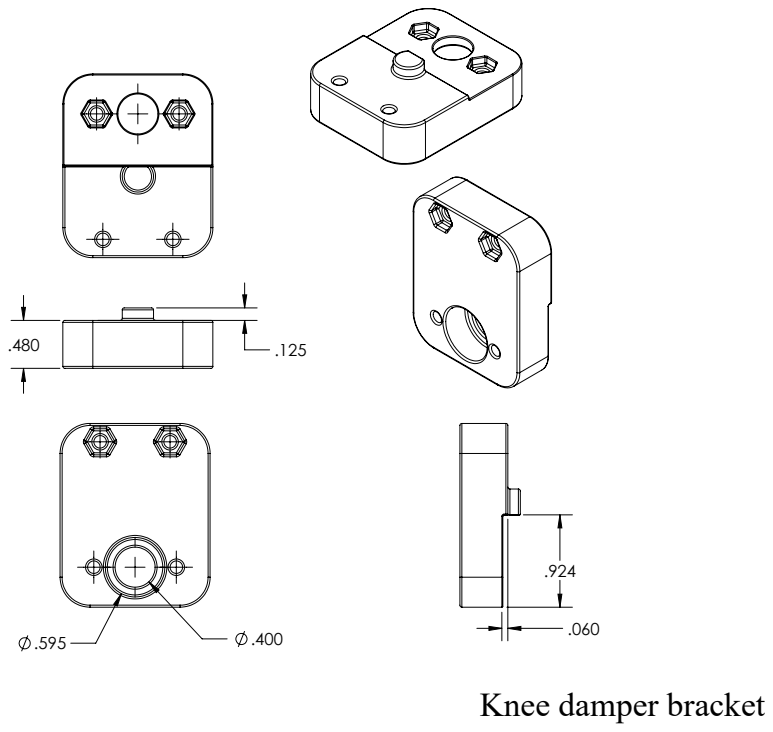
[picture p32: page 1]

Knee damper bracket

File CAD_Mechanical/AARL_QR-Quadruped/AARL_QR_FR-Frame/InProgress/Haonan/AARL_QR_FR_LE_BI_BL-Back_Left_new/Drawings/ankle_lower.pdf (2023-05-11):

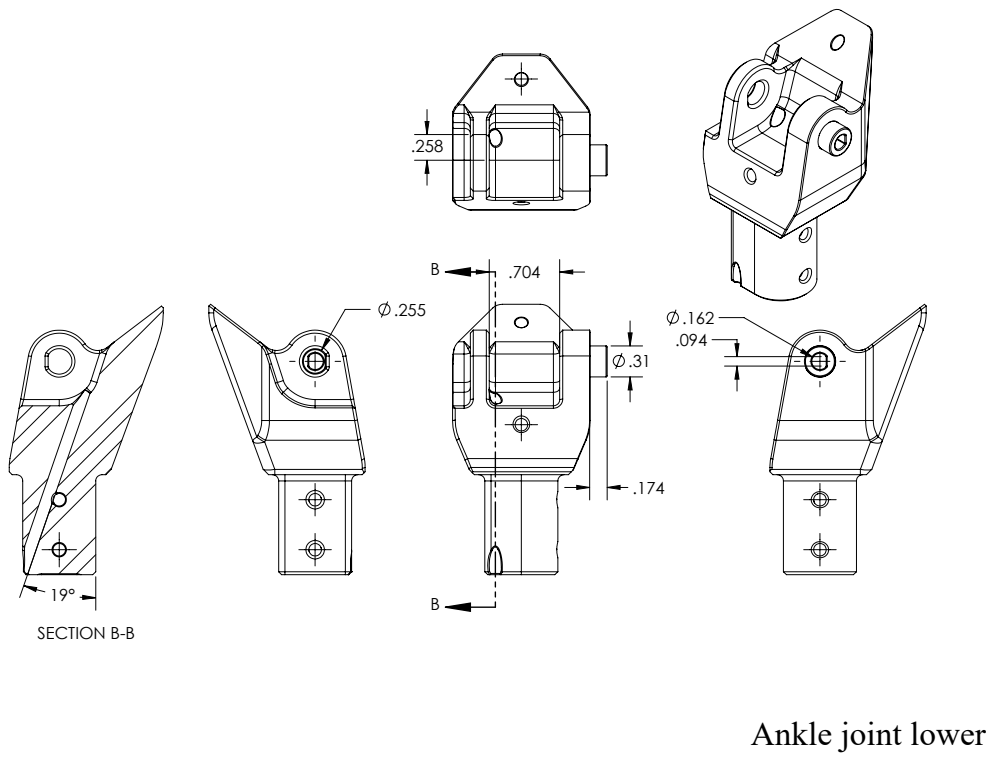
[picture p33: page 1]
SECTION B-B

Ankle joint lower

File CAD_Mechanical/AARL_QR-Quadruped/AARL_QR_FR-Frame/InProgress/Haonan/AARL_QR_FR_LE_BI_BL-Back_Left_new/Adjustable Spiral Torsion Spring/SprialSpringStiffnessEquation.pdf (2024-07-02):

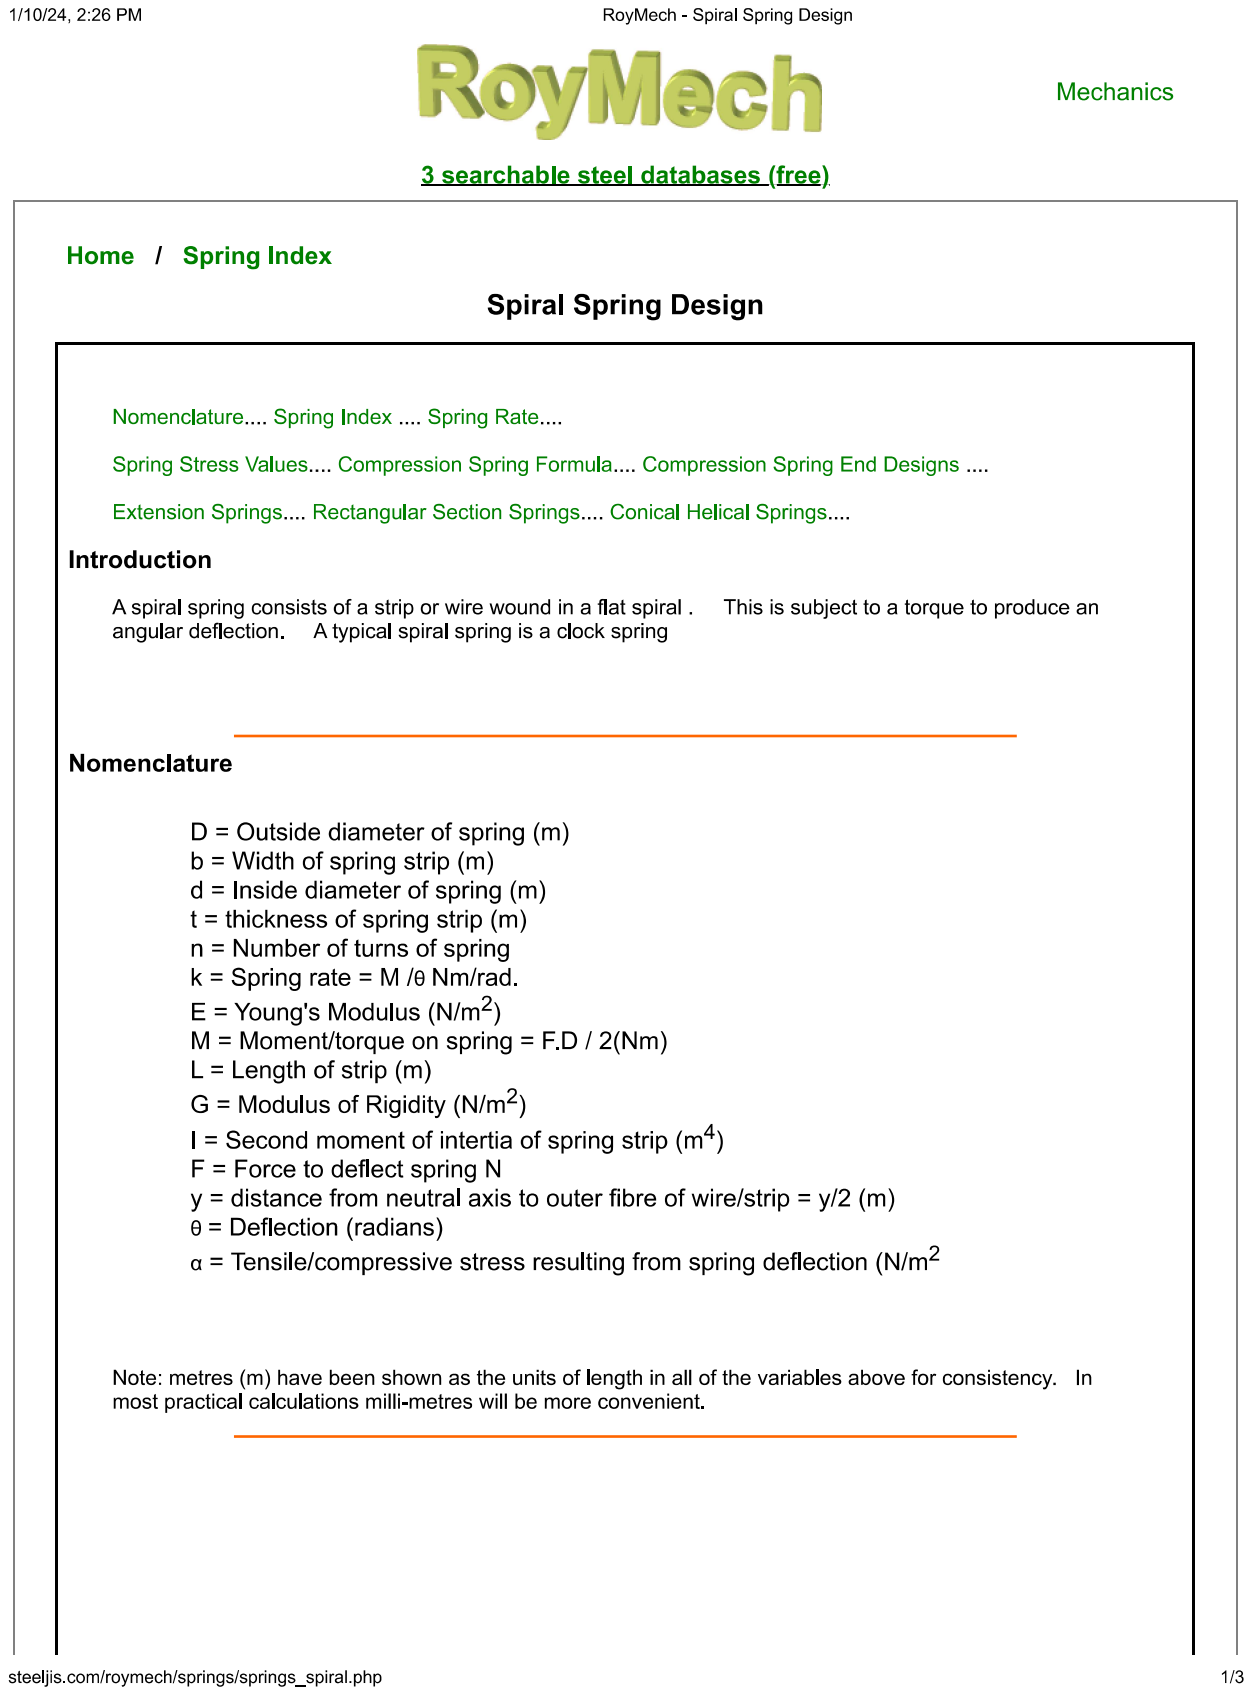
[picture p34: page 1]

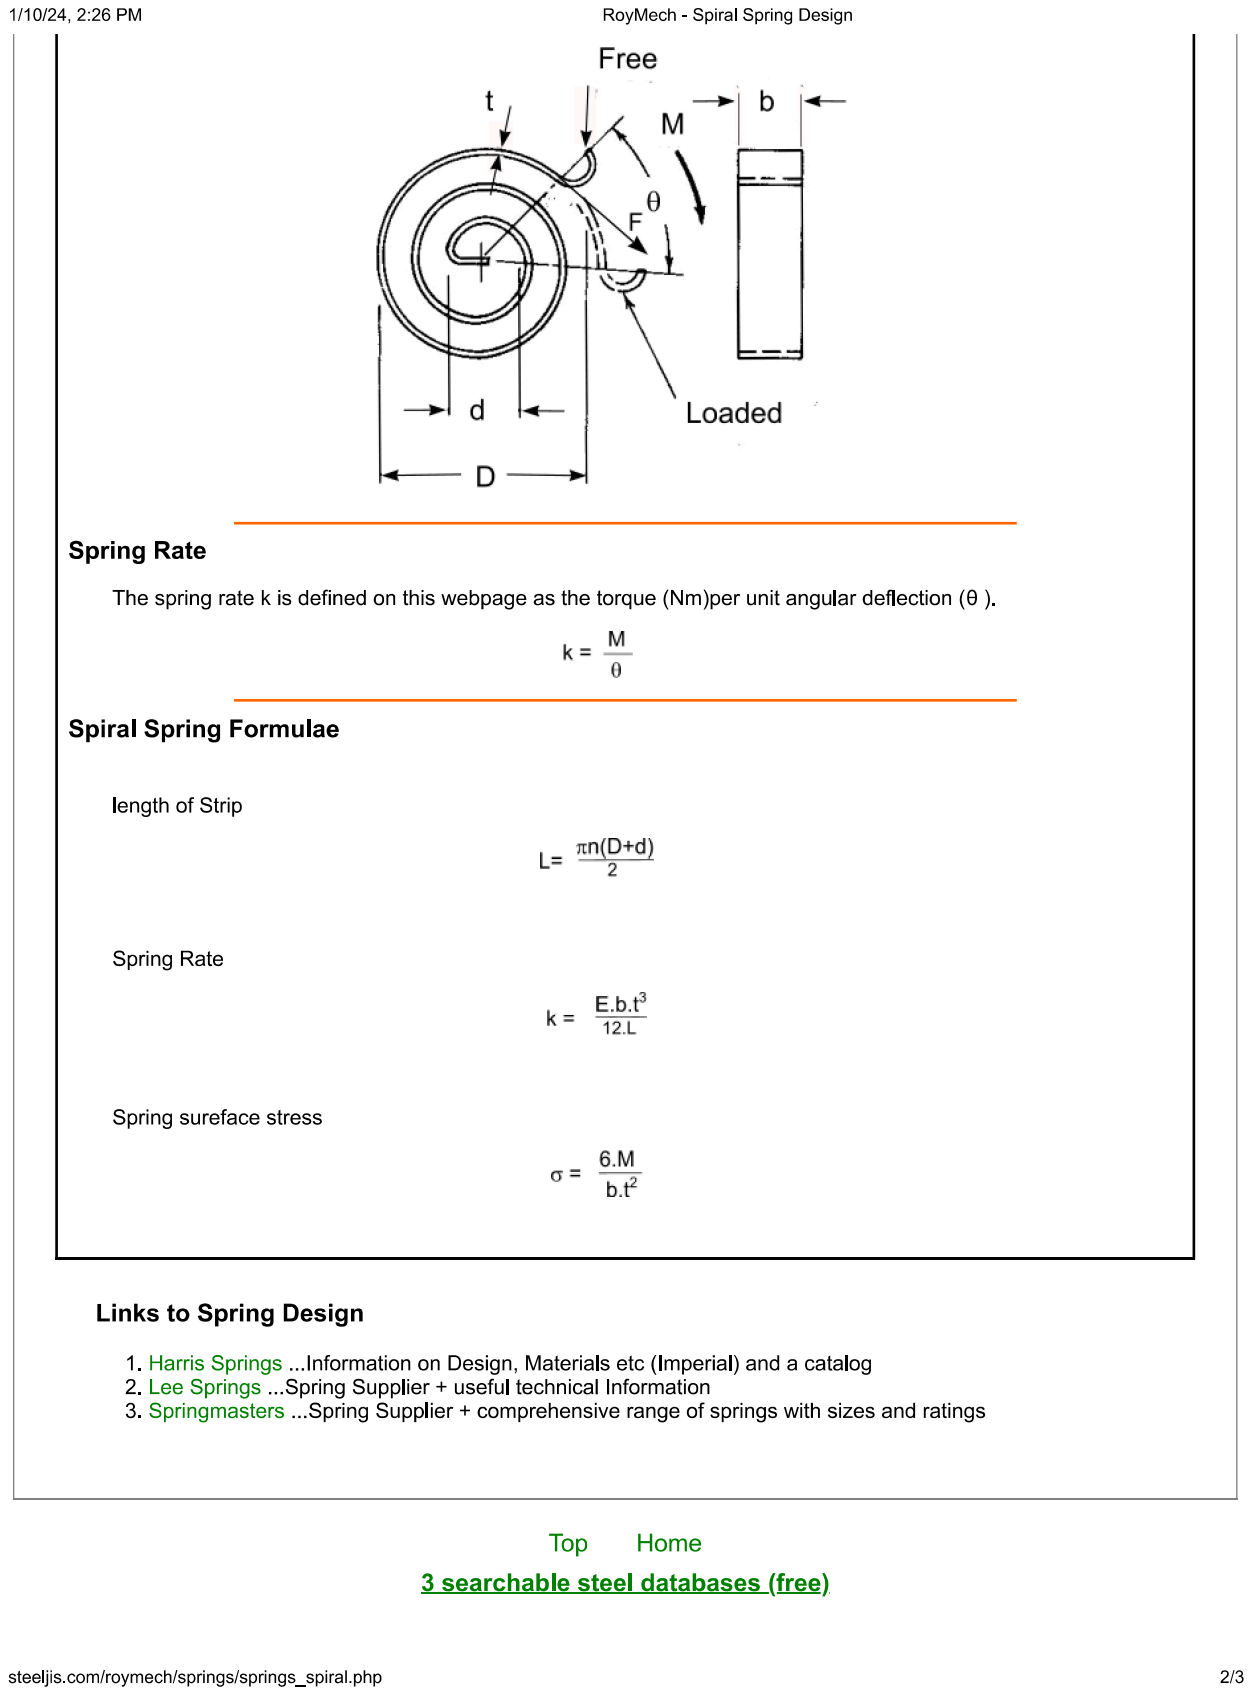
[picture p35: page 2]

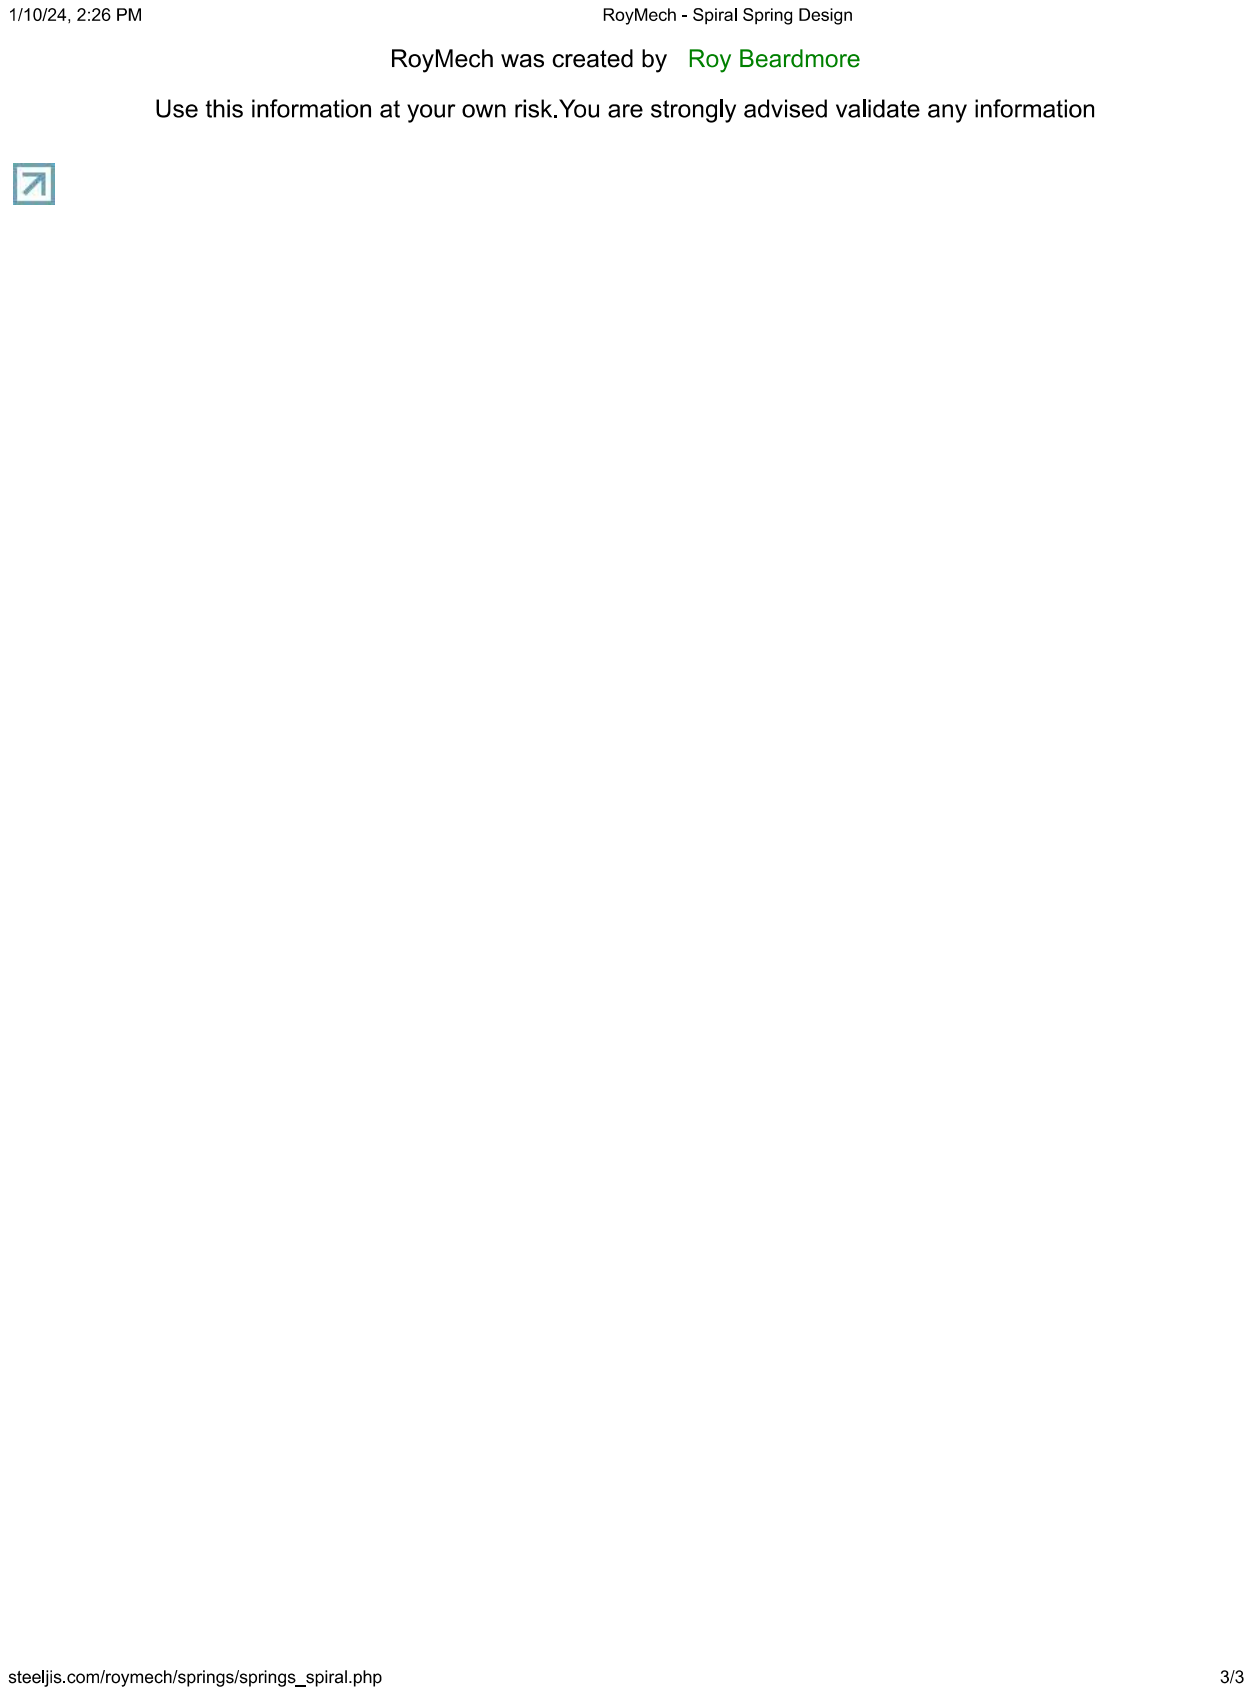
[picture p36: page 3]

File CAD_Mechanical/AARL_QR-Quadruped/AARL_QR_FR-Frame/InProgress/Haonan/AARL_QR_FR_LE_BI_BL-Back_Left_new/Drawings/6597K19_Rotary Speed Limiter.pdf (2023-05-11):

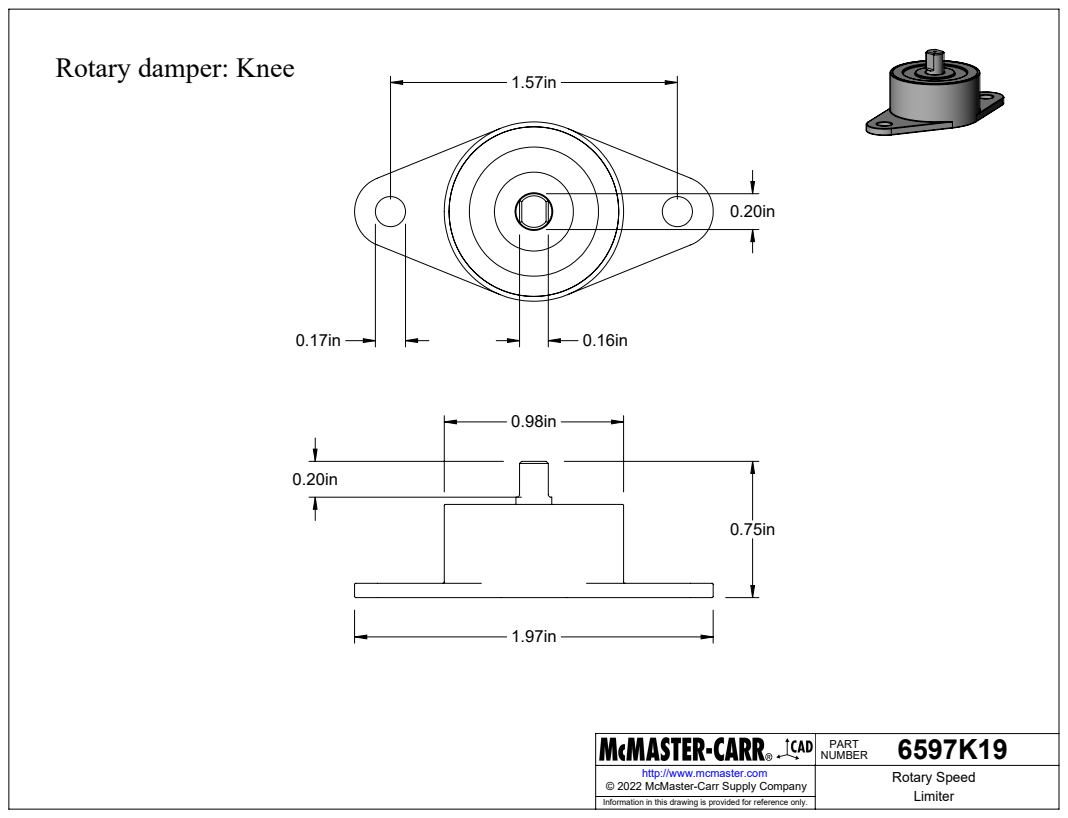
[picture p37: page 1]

Rotary damper: Knee

6597K19 PART NUMBER

http://www.mcmaster.com | Rotary Speed Limiter © 2022 McMaster-Carr Supply Company

Information in this drawing is provided for reference only.

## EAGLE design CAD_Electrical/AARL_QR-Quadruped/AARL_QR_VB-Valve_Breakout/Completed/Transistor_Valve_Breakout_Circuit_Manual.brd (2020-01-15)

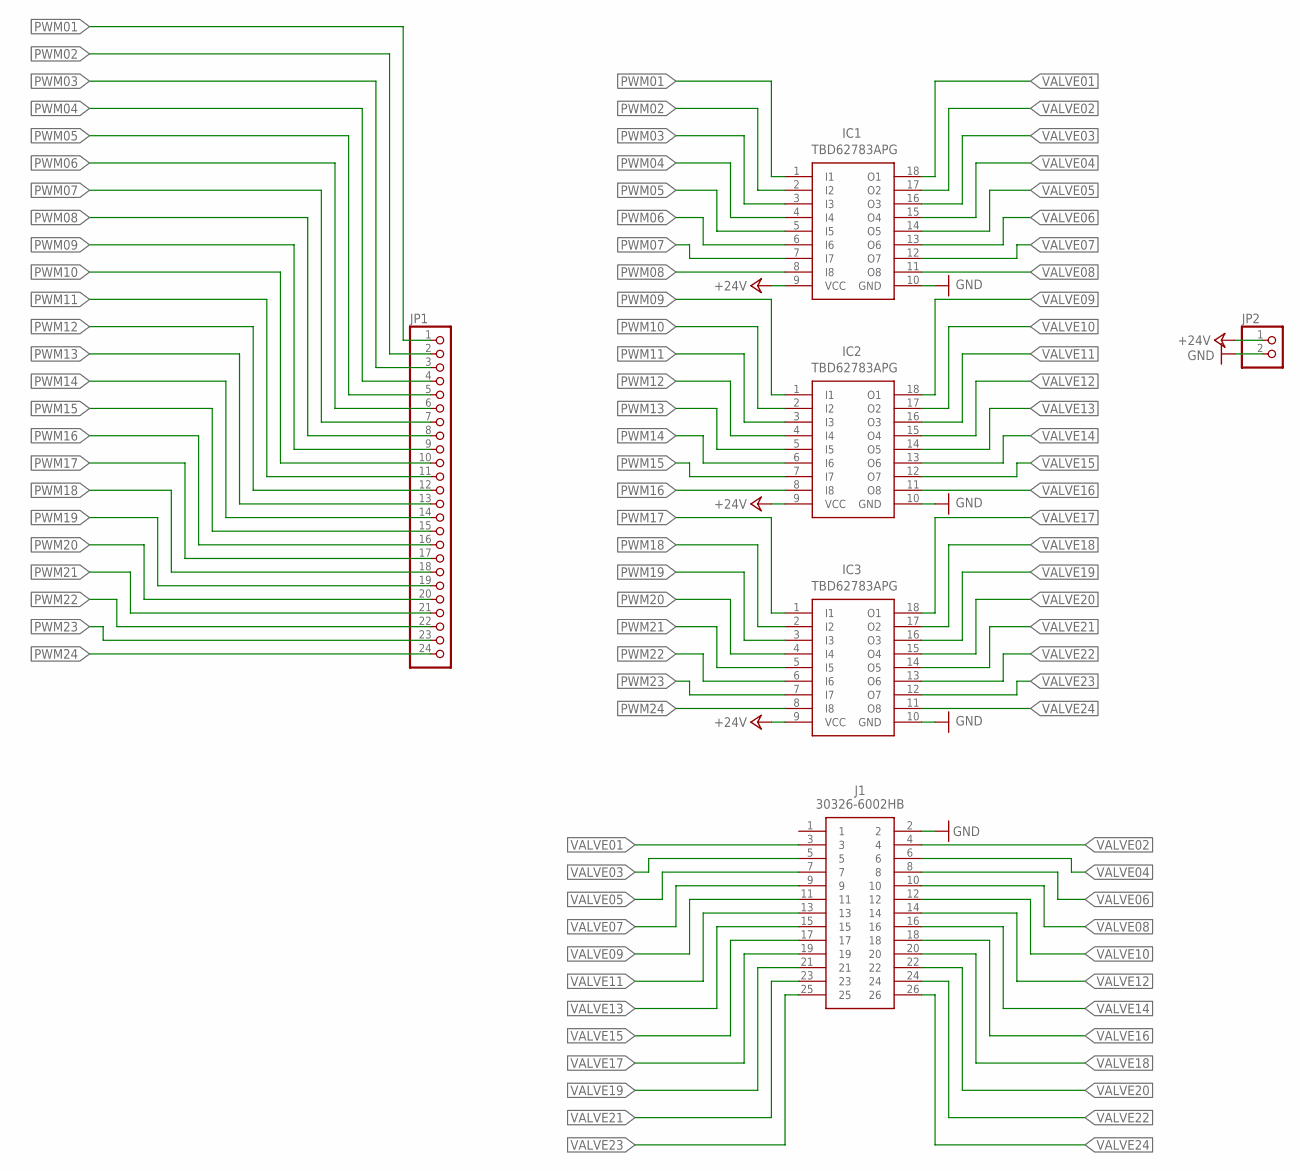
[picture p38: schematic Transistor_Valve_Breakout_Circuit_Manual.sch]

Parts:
IC1, IC2, IC3: TBD62783APG; DIP762W55P254L2286H480Q18N
J1: 30326-6002HB; SHDR26W81P254_2X13_4060X840X94
JP1: PINHD-1X24; 1X24
JP2: PINHD-1X2; 1X02

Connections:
+24V: IC1.9 (VCC), IC2.9 (VCC), IC3.9 (VCC), JP2.1
GND: IC1.10 (GND), IC2.10 (GND), IC3.10 (GND), J1.2, JP2.2
PWM01: IC1.1 (I1), JP1.1
PWM02: IC1.2 (I2), JP1.2
PWM03: IC1.3 (I3), JP1.3
PWM04: IC1.4 (I4), JP1.4
PWM05: IC1.5 (I5), JP1.5
PWM06: IC1.6 (I6), JP1.6
PWM07: IC1.7 (I7), JP1.7
PWM08: IC1.8 (I8), JP1.8
PWM09: IC2.1 (I1), JP1.9
PWM10: IC2.2 (I2), JP1.10
PWM11: IC2.3 (I3), JP1.11
PWM12: IC2.4 (I4), JP1.12
PWM13: IC2.5 (I5), JP1.13
PWM14: IC2.6 (I6), JP1.14
PWM15: IC2.7 (I7), JP1.15
PWM16: IC2.8 (I8), JP1.16
PWM17: IC3.1 (I1), JP1.17
PWM18: IC3.2 (I2), JP1.18
PWM19: IC3.3 (I3), JP1.19
PWM20: IC3.4 (I4), JP1.20
PWM21: IC3.5 (I5), JP1.21
PWM22: IC3.6 (I6), JP1.22
PWM23: IC3.7 (I7), JP1.23
PWM24: IC3.8 (I8), JP1.24
VALVE01: IC1.18 (O1), J1.3
VALVE02: IC1.17 (O2), J1.4
VALVE03: IC1.16 (O3), J1.5
VALVE04: IC1.15 (O4), J1.6
VALVE05: IC1.14 (O5), J1.7
VALVE06: IC1.13 (O6), J1.8
VALVE07: IC1.12 (O7), J1.9
VALVE08: IC1.11 (O8), J1.10
VALVE09: IC2.18 (O1), J1.11
VALVE10: IC2.17 (O2), J1.12
VALVE11: IC2.16 (O3), J1.13
VALVE12: IC2.15 (O4), J1.14
VALVE13: IC2.14 (O5), J1.15
VALVE14: IC2.13 (O6), J1.16
VALVE15: IC2.12 (O7), J1.17
VALVE16: IC2.11 (O8), J1.18
VALVE17: IC3.18 (O1), J1.19
VALVE18: IC3.17 (O2), J1.20
VALVE19: IC3.16 (O3), J1.21
VALVE20: IC3.15 (O4), J1.22
VALVE21: IC3.14 (O5), J1.23
VALVE22: IC3.13 (O6), J1.24
VALVE23: IC3.12 (O7), J1.25
VALVE24: IC3.11 (O8), J1.26

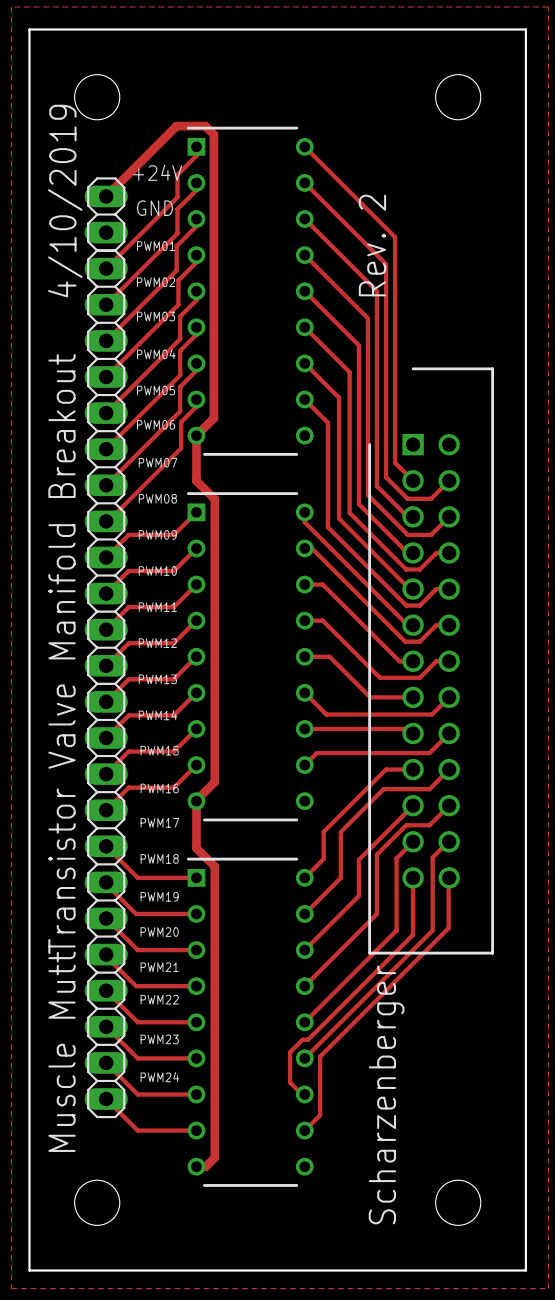
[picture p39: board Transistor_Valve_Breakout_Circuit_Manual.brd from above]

Board: 2 copper layers, 34.9 x 87.3 mm, 6 parts (0 on the bottom side), 50 nets.

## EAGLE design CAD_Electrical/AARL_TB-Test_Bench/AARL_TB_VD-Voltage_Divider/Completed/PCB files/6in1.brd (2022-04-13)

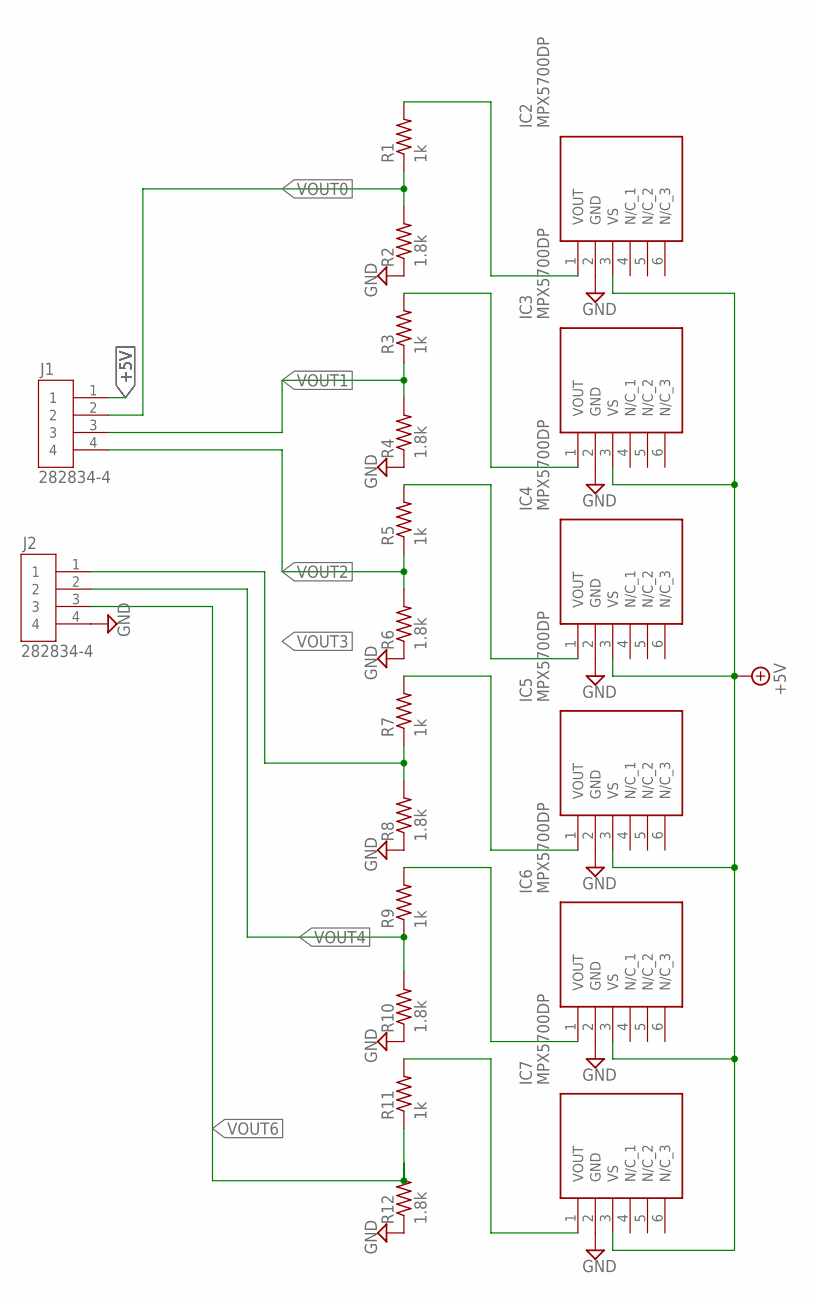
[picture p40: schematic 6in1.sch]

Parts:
IC2, IC3, IC4, IC5, IC6, IC7: MPX5700DP
J1, J2: 282834-4; HDRV4W85P254_4X1_1062X650X1000
R1, R3, R5, R7, R9, R11: 1k; 0204V
R2, R4, R6, R8, R10, R12: 1.8k; 0204V

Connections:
+5V: IC2.3 (VS), IC3.3 (VS), IC4.3 (VS), IC5.3 (VS), IC6.3 (VS), IC7.3 (VS), J1.1
GND: IC2.2 (GND), IC3.2 (GND), IC4.2 (GND), IC5.2 (GND), IC6.2 (GND), IC7.2 (GND), J2.4, R2.1, R4.1, R6.1, R8.1, R10.1, R12.1
unnamed: IC2.1 (VOUT), R1.2
unnamed: IC3.1 (VOUT), R3.2
unnamed: IC4.1 (VOUT), R5.2
unnamed: IC5.1 (VOUT), R7.2
unnamed: IC6.1 (VOUT), R9.2
unnamed: IC7.1 (VOUT), R11.2
VOUT0: J1.2, R1.1, R2.2
VOUT1: J1.3, R3.1, R4.2
VOUT2: J1.4, R5.1, R6.2
VOUT3: J2.1, R7.1, R8.2
VOUT4: J2.2, R9.1, R10.2
VOUT6: J2.3, R11.1, R12.2

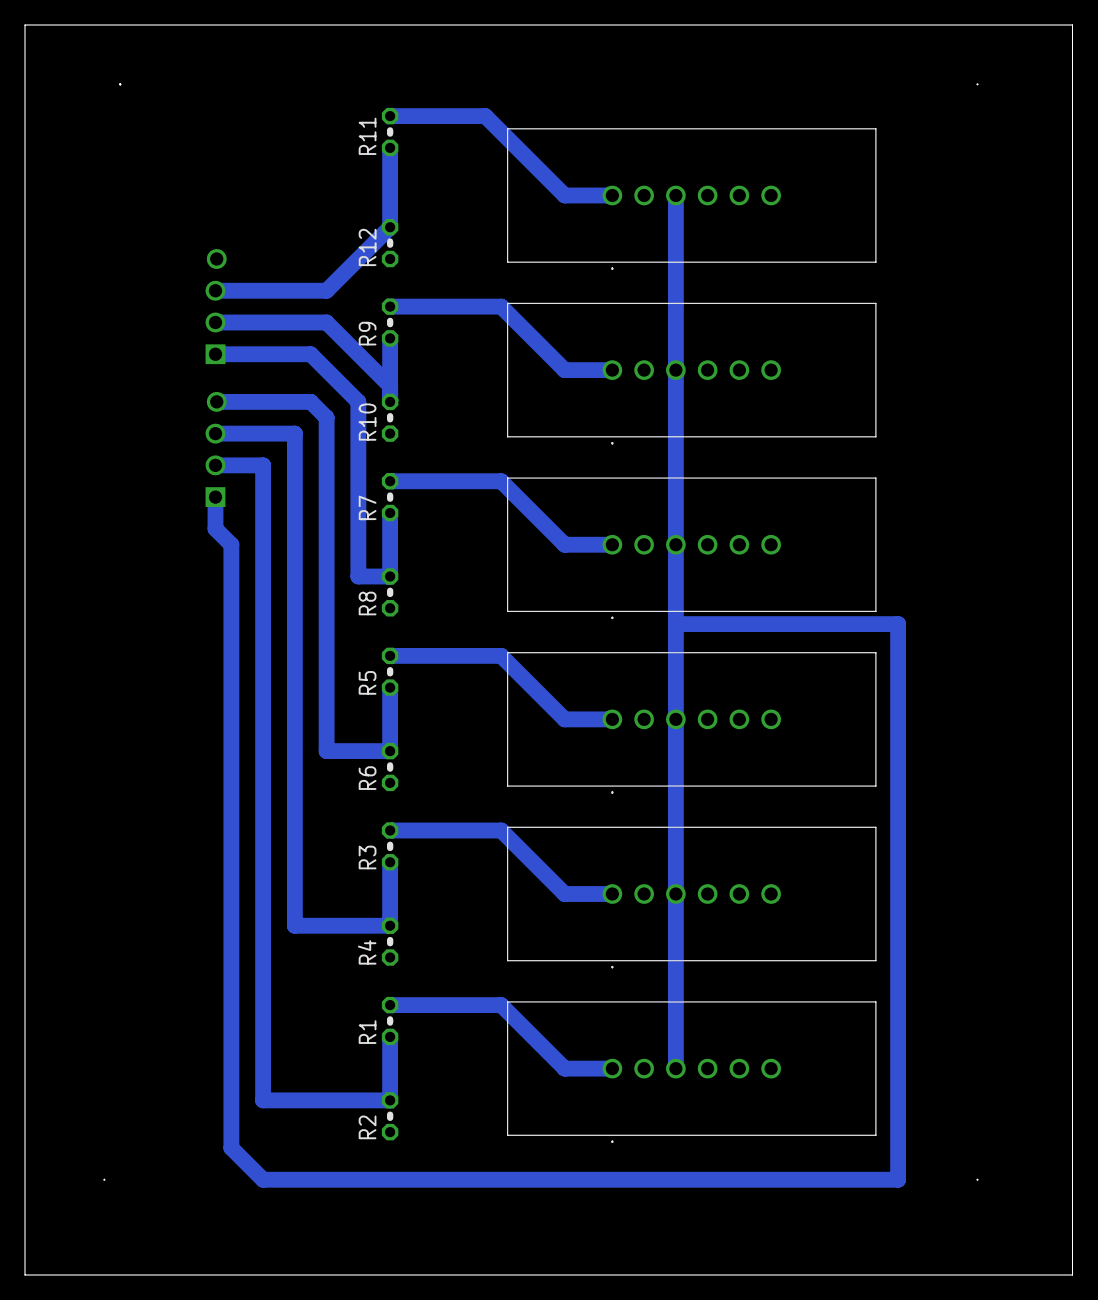
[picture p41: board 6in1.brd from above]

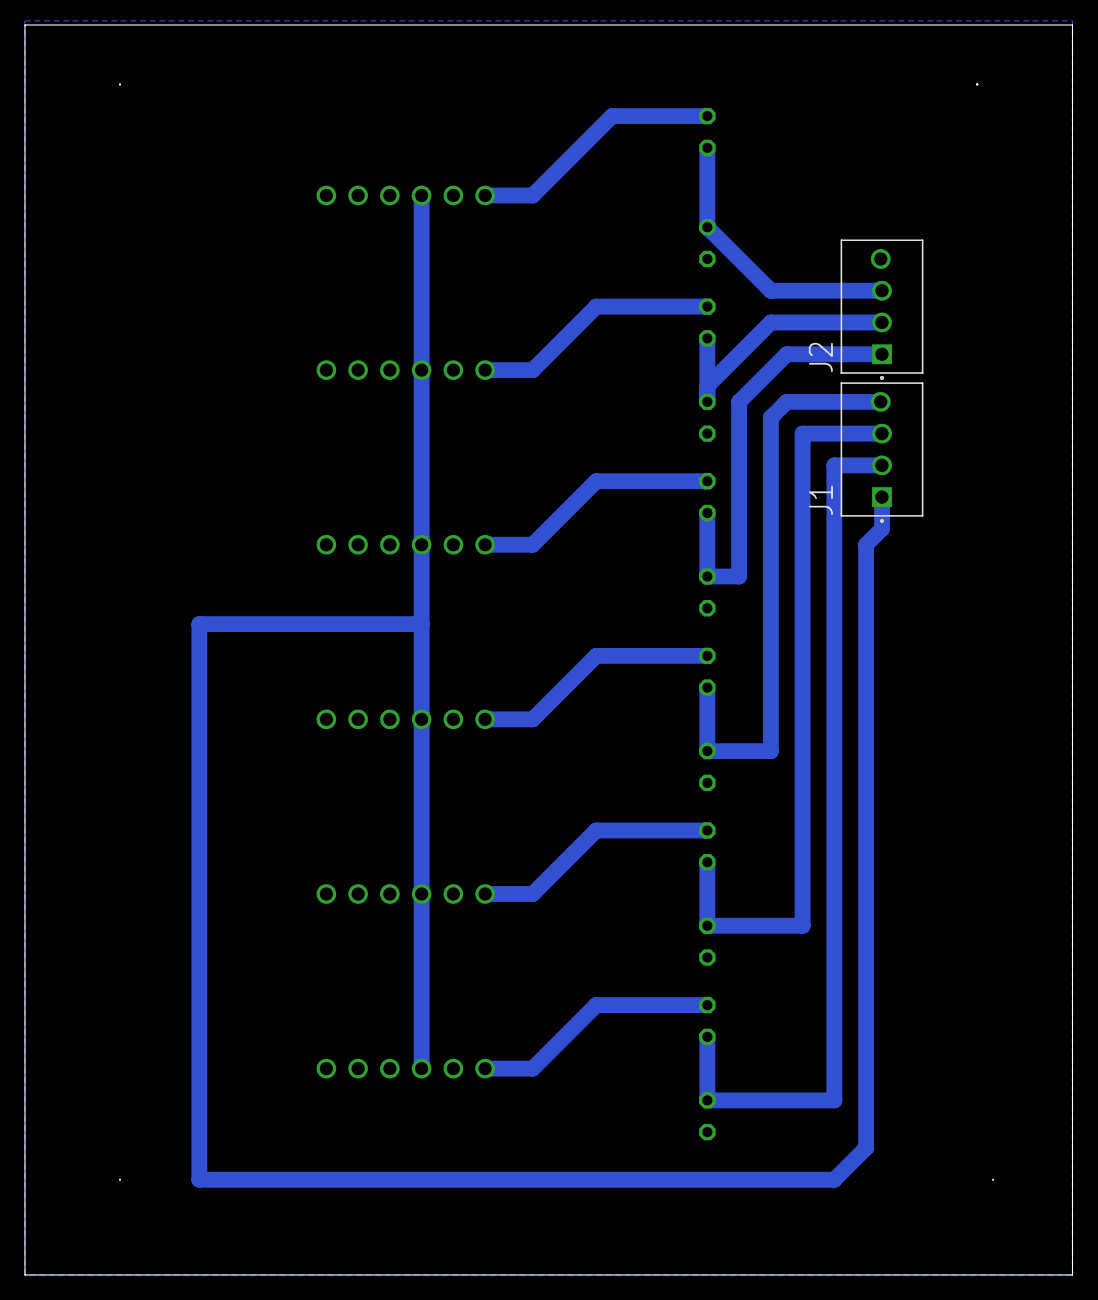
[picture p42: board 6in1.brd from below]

Board: 2 copper layers, 83.8 x 100.0 mm, 20 parts (2 on the bottom side), 14 nets.

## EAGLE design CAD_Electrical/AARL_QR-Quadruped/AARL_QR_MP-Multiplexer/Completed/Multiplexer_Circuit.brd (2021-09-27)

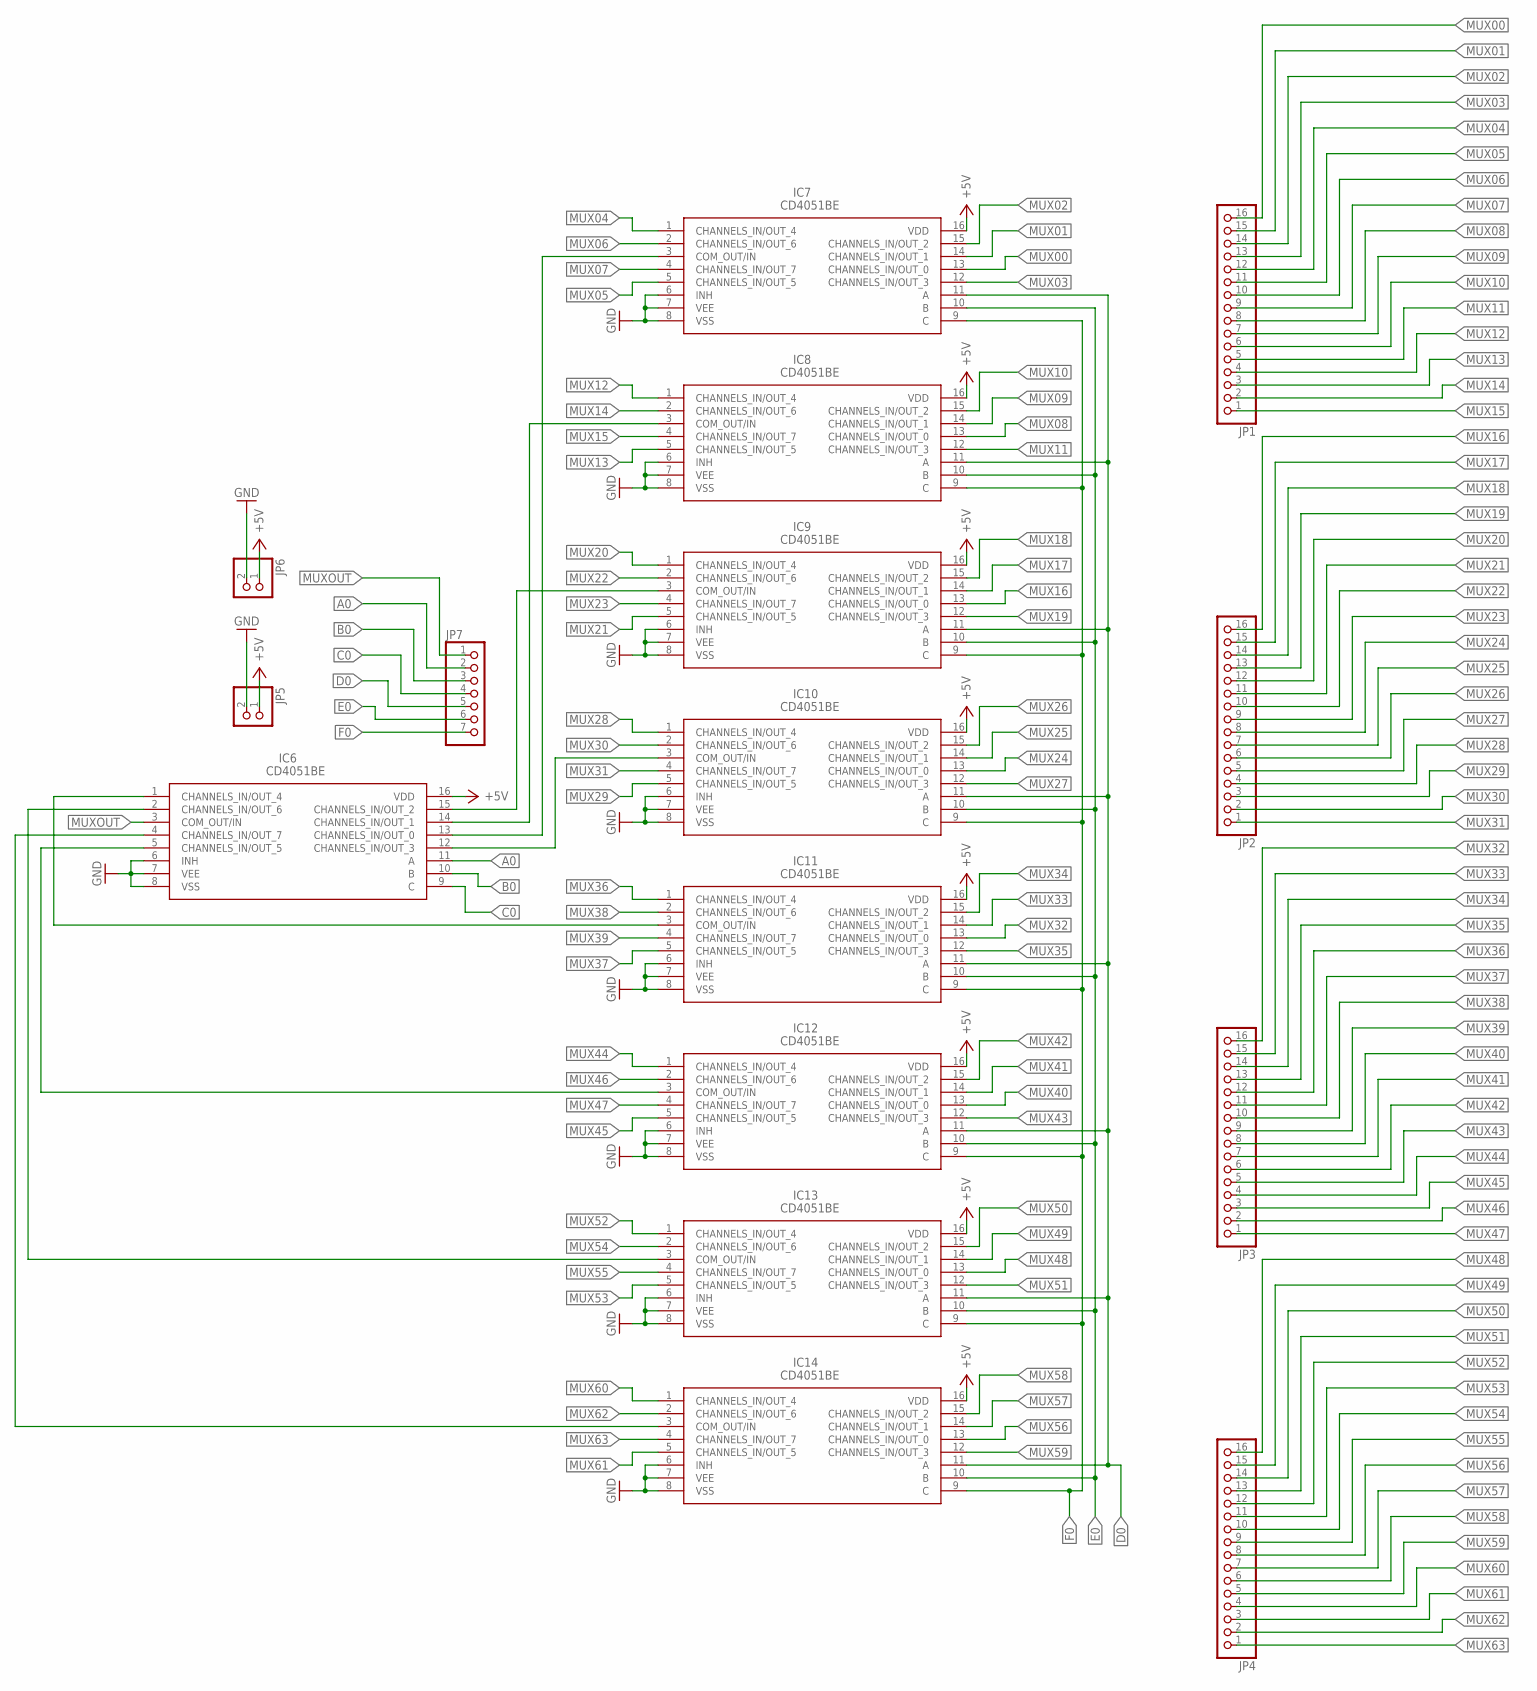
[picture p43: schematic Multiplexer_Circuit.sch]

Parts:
IC6, IC7, IC8, IC9, IC10, IC11, IC12, IC13, IC14: CD4051BE; DIP254P762X508-16
JP1, JP2, JP3, JP4: PINHD-1X16; 1X16
JP5, JP6: PINHD-1X2; 1X02
JP7: PINHD-1X7; 1X07

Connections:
+5V: IC6.16 (VDD), IC7.16 (VDD), IC8.16 (VDD), IC9.16 (VDD), IC10.16 (VDD), IC11.16 (VDD), IC12.16 (VDD), IC13.16 (VDD), IC14.16 (VDD), JP5.1, JP6.1
A0: IC6.11 (A), JP7.2
B0: IC6.10 (B), JP7.3
C0: IC6.9 (C), JP7.4
D0: IC7.11 (A), IC8.11 (A), IC9.11 (A), IC10.11 (A), IC11.11 (A), IC12.11 (A), IC13.11 (A), IC14.11 (A), JP7.5
E0: IC7.10 (B), IC8.10 (B), IC9.10 (B), IC10.10 (B), IC11.10 (B), IC12.10 (B), IC13.10 (B), IC14.10 (B), JP7.6
F0: IC7.9 (C), IC8.9 (C), IC9.9 (C), IC10.9 (C), IC11.9 (C), IC12.9 (C), IC13.9 (C), IC14.9 (C), JP7.7
GND: IC6.6 (INH), IC6.7 (VEE), IC6.8 (VSS), IC7.6 (INH), IC7.7 (VEE), IC7.8 (VSS), IC8.6 (INH), IC8.7 (VEE), IC8.8 (VSS), IC9.6 (INH), IC9.7 (VEE), IC9.8 (VSS), IC10.6 (INH), IC10.7 (VEE), IC10.8 (VSS), IC11.6 (INH), IC11.7 (VEE), IC11.8 (VSS), IC12.6 (INH), IC12.7 (VEE), IC12.8 (VSS), IC13.6 (INH), IC13.7 (VEE), IC13.8 (VSS), IC14.6 (INH), IC14.7 (VEE), IC14.8 (VSS), JP5.2, JP6.2
MUX00: IC7.13 (CHANNELS_IN/OUT_0), JP1.16
MUX01: IC7.14 (CHANNELS_IN/OUT_1), JP1.15
MUX02: IC7.15 (CHANNELS_IN/OUT_2), JP1.14
MUX03: IC7.12 (CHANNELS_IN/OUT_3), JP1.13
MUX04: IC7.1 (CHANNELS_IN/OUT_4), JP1.12
MUX05: IC7.5 (CHANNELS_IN/OUT_5), JP1.11
MUX06: IC7.2 (CHANNELS_IN/OUT_6), JP1.10
MUX07: IC7.4 (CHANNELS_IN/OUT_7), JP1.9
MUX08: IC8.13 (CHANNELS_IN/OUT_0), JP1.8
MUX09: IC8.14 (CHANNELS_IN/OUT_1), JP1.7
MUX10: IC8.15 (CHANNELS_IN/OUT_2), JP1.6
MUX11: IC8.12 (CHANNELS_IN/OUT_3), JP1.5
MUX12: IC8.1 (CHANNELS_IN/OUT_4), JP1.4
MUX13: IC8.5 (CHANNELS_IN/OUT_5), JP1.3
MUX14: IC8.2 (CHANNELS_IN/OUT_6), JP1.2
MUX15: IC8.4 (CHANNELS_IN/OUT_7), JP1.1
MUX16: IC9.13 (CHANNELS_IN/OUT_0), JP2.16
MUX17: IC9.14 (CHANNELS_IN/OUT_1), JP2.15
MUX18: IC9.15 (CHANNELS_IN/OUT_2), JP2.14
MUX19: IC9.12 (CHANNELS_IN/OUT_3), JP2.13
MUX20: IC9.1 (CHANNELS_IN/OUT_4), JP2.12
MUX21: IC9.5 (CHANNELS_IN/OUT_5), JP2.11
MUX22: IC9.2 (CHANNELS_IN/OUT_6), JP2.10
MUX23: IC9.4 (CHANNELS_IN/OUT_7), JP2.9
MUX24: IC10.13 (CHANNELS_IN/OUT_0), JP2.8
MUX25: IC10.14 (CHANNELS_IN/OUT_1), JP2.7
MUX26: IC10.15 (CHANNELS_IN/OUT_2), JP2.6
MUX27: IC10.12 (CHANNELS_IN/OUT_3), JP2.5
MUX28: IC10.1 (CHANNELS_IN/OUT_4), JP2.4
MUX29: IC10.5 (CHANNELS_IN/OUT_5), JP2.3
MUX30: IC10.2 (CHANNELS_IN/OUT_6), JP2.2
MUX31: IC10.4 (CHANNELS_IN/OUT_7), JP2.1
MUX32: IC11.13 (CHANNELS_IN/OUT_0), JP3.16
MUX33: IC11.14 (CHANNELS_IN/OUT_1), JP3.15
MUX34: IC11.15 (CHANNELS_IN/OUT_2), JP3.14
MUX35: IC11.12 (CHANNELS_IN/OUT_3), JP3.13
MUX36: IC11.1 (CHANNELS_IN/OUT_4), JP3.12
MUX37: IC11.5 (CHANNELS_IN/OUT_5), JP3.11
MUX38: IC11.2 (CHANNELS_IN/OUT_6), JP3.10
MUX39: IC11.4 (CHANNELS_IN/OUT_7), JP3.9
MUX40: IC12.13 (CHANNELS_IN/OUT_0), JP3.8
MUX41: IC12.14 (CHANNELS_IN/OUT_1), JP3.7
MUX42: IC12.15 (CHANNELS_IN/OUT_2), JP3.6
MUX43: IC12.12 (CHANNELS_IN/OUT_3), JP3.5
MUX44: IC12.1 (CHANNELS_IN/OUT_4), JP3.4
MUX45: IC12.5 (CHANNELS_IN/OUT_5), JP3.3
MUX46: IC12.2 (CHANNELS_IN/OUT_6), JP3.2
MUX47: IC12.4 (CHANNELS_IN/OUT_7), JP3.1
MUX48: IC13.13 (CHANNELS_IN/OUT_0), JP4.16
MUX49: IC13.14 (CHANNELS_IN/OUT_1), JP4.15
MUX50: IC13.15 (CHANNELS_IN/OUT_2), JP4.14
MUX51: IC13.12 (CHANNELS_IN/OUT_3), JP4.13
MUX52: IC13.1 (CHANNELS_IN/OUT_4), JP4.12
MUX53: IC13.5 (CHANNELS_IN/OUT_5), JP4.11
MUX54: IC13.2 (CHANNELS_IN/OUT_6), JP4.10
MUX55: IC13.4 (CHANNELS_IN/OUT_7), JP4.9
MUX56: IC14.13 (CHANNELS_IN/OUT_0), JP4.8
MUX57: IC14.14 (CHANNELS_IN/OUT_1), JP4.7
MUX58: IC14.15 (CHANNELS_IN/OUT_2), JP4.6
MUX59: IC14.12 (CHANNELS_IN/OUT_3), JP4.5
MUX60: IC14.1 (CHANNELS_IN/OUT_4), JP4.4
MUX61: IC14.5 (CHANNELS_IN/OUT_5), JP4.3
MUX62: IC14.2 (CHANNELS_IN/OUT_6), JP4.2
MUX63: IC14.4 (CHANNELS_IN/OUT_7), JP4.1
MUXOUT: IC6.3 (COM_OUT/IN), JP7.1
unnamed: IC6.13 (CHANNELS_IN/OUT_0), IC7.3 (COM_OUT/IN)
unnamed: IC6.14 (CHANNELS_IN/OUT_1), IC8.3 (COM_OUT/IN)
unnamed: IC6.15 (CHANNELS_IN/OUT_2), IC9.3 (COM_OUT/IN)
unnamed: IC6.12 (CHANNELS_IN/OUT_3), IC10.3 (COM_OUT/IN)
unnamed: IC6.1 (CHANNELS_IN/OUT_4), IC11.3 (COM_OUT/IN)
unnamed: IC6.5 (CHANNELS_IN/OUT_5), IC12.3 (COM_OUT/IN)
unnamed: IC6.2 (CHANNELS_IN/OUT_6), IC13.3 (COM_OUT/IN)
unnamed: IC6.4 (CHANNELS_IN/OUT_7), IC14.3 (COM_OUT/IN)

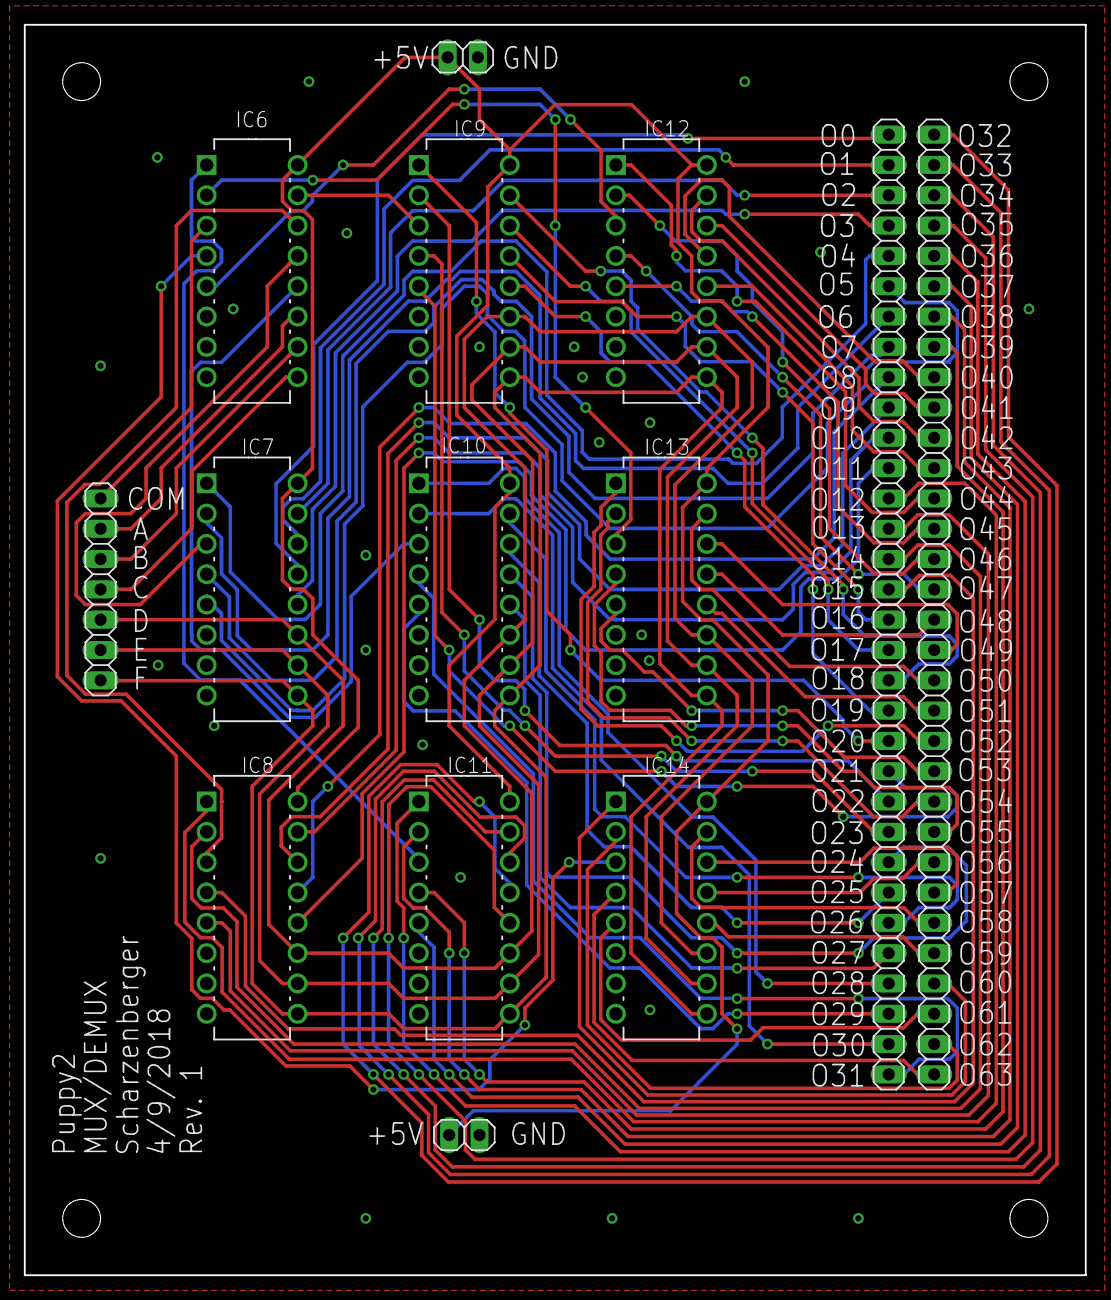
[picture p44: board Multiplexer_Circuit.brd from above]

Board: 2 copper layers, 88.9 x 104.8 mm, 16 parts (0 on the bottom side), 81 nets.

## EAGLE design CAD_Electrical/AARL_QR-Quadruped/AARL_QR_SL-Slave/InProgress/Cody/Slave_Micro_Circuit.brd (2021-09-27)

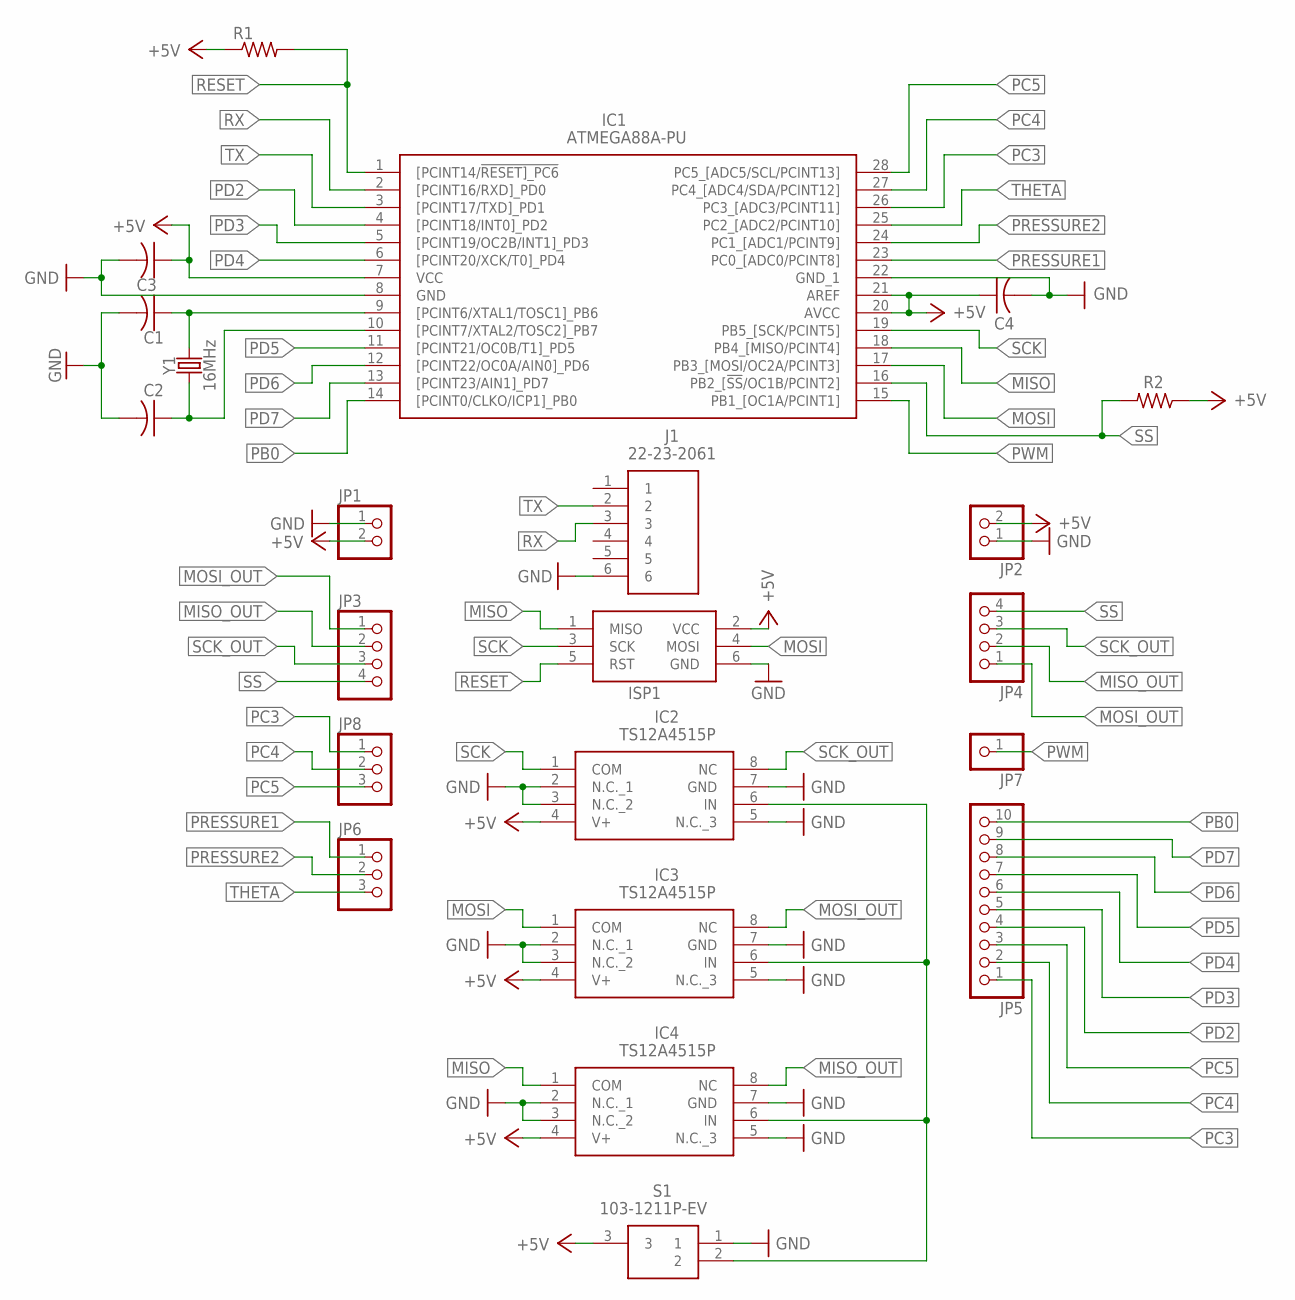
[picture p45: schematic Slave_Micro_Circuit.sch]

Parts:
C1, C2, C3, C4: C-US050-030X075; C050-030X075
IC1: ATMEGA88A-PU; DIP794W53P254L3467H457Q28N
IC2, IC3, IC4: TS12A4515P; DIP794W46P254L959H508Q8N
ISP1: AVRISP-BOX
J1: 22-23-2061; SHDR6W87P0X254_1X6_1509X635X10
JP1, JP2: PINHD-1X2; 1X02
JP3, JP4: PINHD-1X4; 1X04
JP5: PINHD-1X10; 1X10
JP6, JP8: PINHD-1X3; 1X03
JP7: PINHD-1X1; 1X01
R1, R2: R-US_0207/10; 0207/10
S1: 103-1211P-EV; 1031211PEV
Y1: 16MHz; HC49US

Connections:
+5V: C3.1, C4.1, IC1.7 (VCC), IC1.20 (AVCC), IC1.21 (AREF), IC2.4 (V+), IC3.4 (V+), IC4.4 (V+), ISP1.2 (VCC), JP1.2, JP2.2, R1.1, R2.1, S1.3
GND: C1.2, C2.2, C3.2, C4.2, IC1.8 (GND), IC1.22 (GND_1), IC2.2 (N.C._1), IC2.3 (N.C._2), IC2.5 (N.C._3), IC2.7 (GND), IC3.2 (N.C._1), IC3.3 (N.C._2), IC3.5 (N.C._3), IC3.7 (GND), IC4.2 (N.C._1), IC4.3 (N.C._2), IC4.5 (N.C._3), IC4.7 (GND), ISP1.6 (GND), J1.6, JP1.1, JP2.1, S1.1
MISO: IC1.18 (PB4_[MISO/PCINT4]), IC4.1 (COM), ISP1.1 (MISO)
MISO_OUT: IC4.8 (NC), JP3.2, JP4.2
MOSI: IC1.17 (PB3_[MOSI/OC2A/PCINT3]), IC3.1 (COM), ISP1.4 (MOSI)
MOSI_OUT: IC3.8 (NC), JP3.1, JP4.1
unnamed: IC2.6 (IN), IC3.6 (IN), IC4.6 (IN), S1.2
unnamed: C2.1, IC1.10 ([PCINT7/XTAL2/TOSC2]_PB7), Y1.1
unnamed: C1.1, IC1.9 ([PCINT6/XTAL1/TOSC1]_PB6), Y1.2
PB0: IC1.14 ([PCINT0/CLKO/ICP1]_PB0), JP5.10
PC3: IC1.26 (PC3_[ADC3/PCINT11]), JP5.1, JP8.1
PC4: IC1.27 (PC4_[ADC4/SDA/PCINT12]), JP5.2, JP8.2
PC5: IC1.28 (PC5_[ADC5/SCL/PCINT13]), JP5.3, JP8.3
PD2: IC1.4 ([PCINT18/INT0]_PD2), JP5.4
PD3: IC1.5 ([PCINT19/OC2B/INT1]_PD3), JP5.5
PD4: IC1.6 ([PCINT20/XCK/T0]_PD4), JP5.6
PD5: IC1.11 ([PCINT21/OC0B/T1]_PD5), JP5.7
PD6: IC1.12 ([PCINT22/OC0A/AIN0]_PD6), JP5.8
PD7: IC1.13 ([PCINT23/AIN1]_PD7), JP5.9
PRESSURE1: IC1.23 (PC0_[ADC0/PCINT8]), JP6.1
PRESSURE2: IC1.24 (PC1_[ADC1/PCINT9]), JP6.2
PWM: IC1.15 (PB1_[OC1A/PCINT1]), JP7.1
RESET: IC1.1 ([PCINT14/!RESET]_PC6), ISP1.5 (RST), R1.2
RX: IC1.2 ([PCINT16/RXD]_PD0), J1.3
SCK: IC1.19 (PB5_[SCK/PCINT5]), IC2.1 (COM), ISP1.3 (SCK)
SCK_OUT: IC2.8 (NC), JP3.3, JP4.3
SS: IC1.16 (PB2_[!SS!/OC1B/PCINT2]), JP3.4, JP4.4, R2.2
THETA: IC1.25 (PC2_[ADC2/PCINT10]), JP6.3
TX: IC1.3 ([PCINT17/TXD]_PD1), J1.2

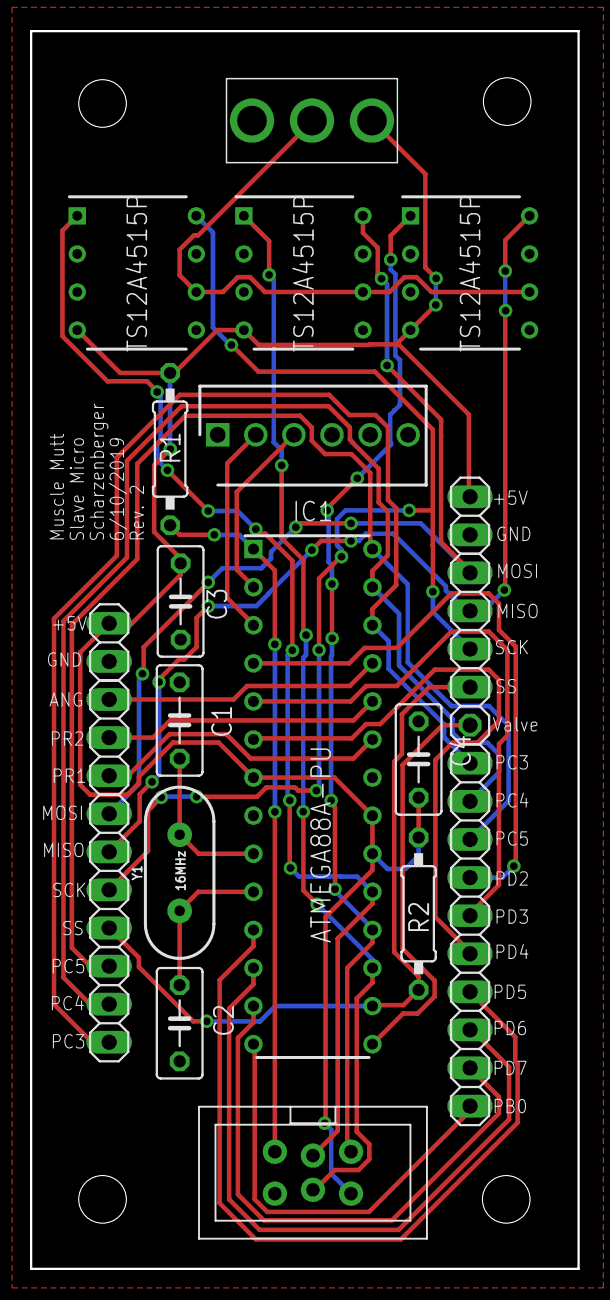
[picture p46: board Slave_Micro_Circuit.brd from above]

Board: 2 copper layers, 36.5 x 82.5 mm, 22 parts (0 on the bottom side), 29 nets.

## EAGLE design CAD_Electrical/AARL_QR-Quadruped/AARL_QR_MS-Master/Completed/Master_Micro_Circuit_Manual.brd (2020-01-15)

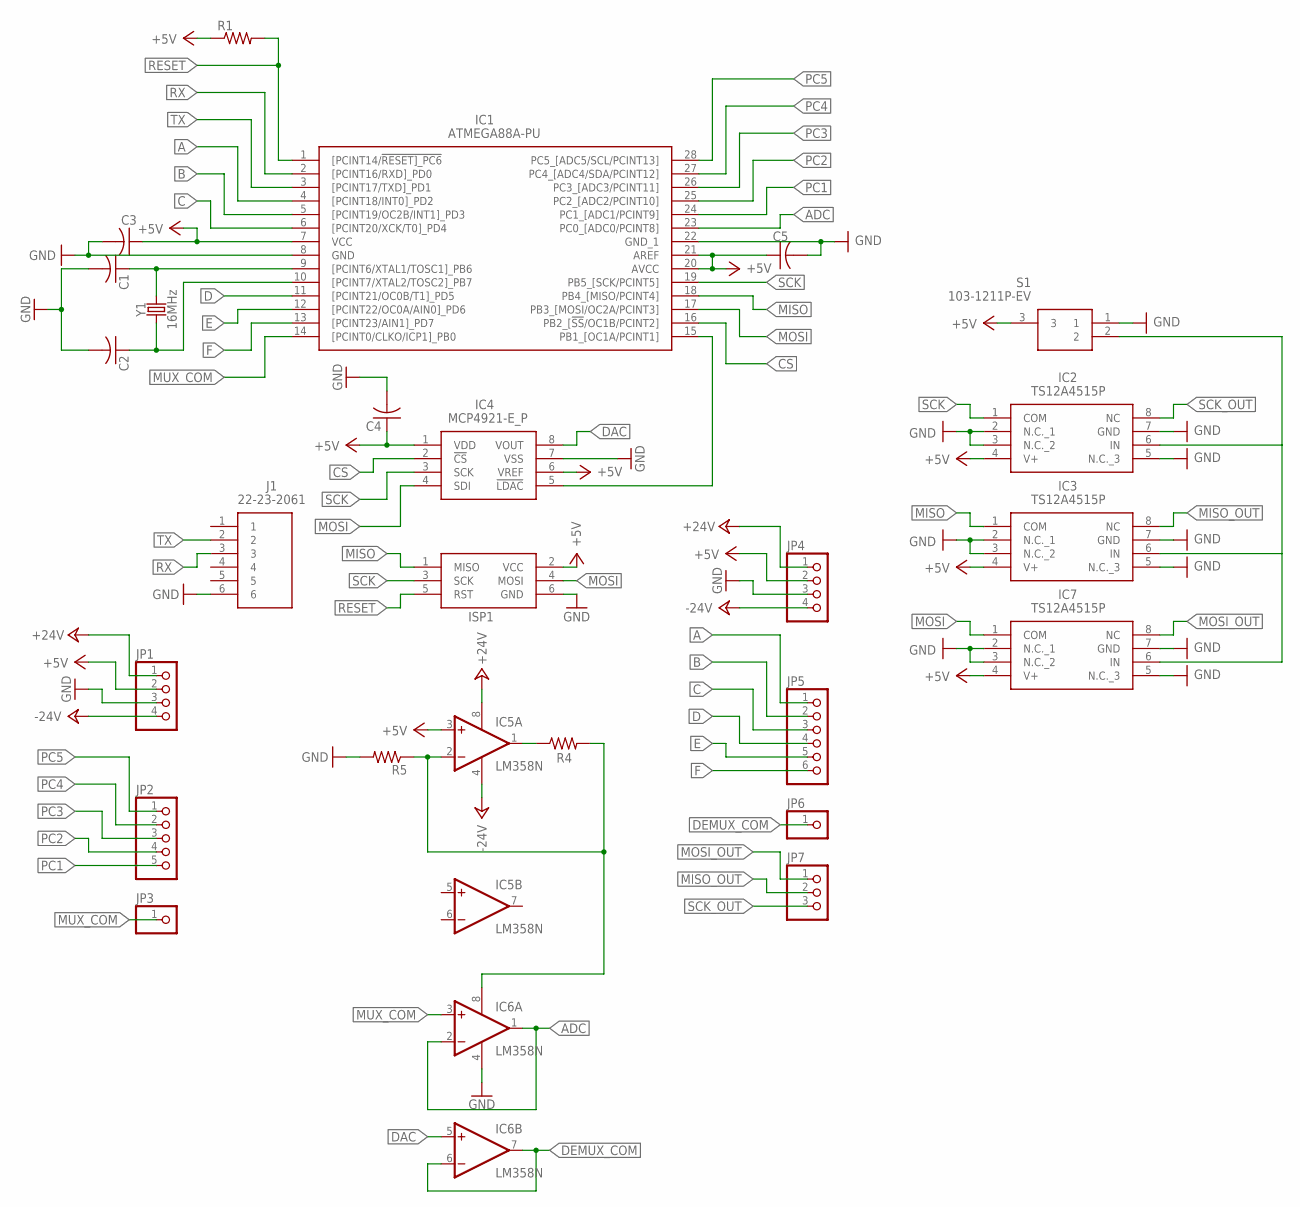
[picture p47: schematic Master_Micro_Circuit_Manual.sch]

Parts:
C1, C2, C3, C4, C5: C-US050-030X075; C050-030X075
IC1: ATMEGA88A-PU; DIP794W53P254L3467H457Q28N
IC2, IC3, IC7: TS12A4515P; DIP794W46P254L959H508Q8N
IC4: MCP4921-E_P; DIP781W56P254L950H533Q8N
IC5, IC6: LM358N; DIL08
ISP1: AVRISP-BOX
J1: 22-23-2061; SHDR6W87P0X254_1X6_1509X635X10
JP1, JP4: PINHD-1X4; 1X04
JP2: PINHD-1X5; 1X05
JP3, JP6: PINHD-1X1; 1X01
JP5: PINHD-1X6; 1X06
JP7: PINHD-1X3; 1X03
R1, R4, R5: R-US_0207/10; 0207/10
S1: 103-1211P-EV; 1031211PEV
Y1: 16MHz; HC49US

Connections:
+5V: C3.1, C4.1, C5.1, IC1.7 (VCC), IC1.20 (AVCC), IC1.21 (AREF), IC2.4 (V+), IC3.4 (V+), IC4.1 (VDD), IC4.6 (VREF), IC5.3 (+IN), IC7.4 (V+), ISP1.2 (VCC), JP1.2, JP4.2, R1.1, S1.3
+24V: IC5.8 (V+), JP1.1, JP4.1
-24V: IC5.4 (V-), JP1.4, JP4.4
A: IC1.4 ([PCINT18/INT0]_PD2), JP5.1
ADC: IC1.23 (PC0_[ADC0/PCINT8]), IC6.1 (OUT), IC6.2 (-IN)
B: IC1.5 ([PCINT19/OC2B/INT1]_PD3), JP5.2
C: IC1.6 ([PCINT20/XCK/T0]_PD4), JP5.3
CS: IC1.16 (PB2_[!SS!/OC1B/PCINT2]), IC4.2 (!CS)
D: IC1.11 ([PCINT21/OC0B/T1]_PD5), JP5.4
DAC: IC4.8 (VOUT), IC6.5 (+IN)
DEMUX_COM: IC6.6 (-IN), IC6.7 (OUT), JP6.1
E: IC1.12 ([PCINT22/OC0A/AIN0]_PD6), JP5.5
F: IC1.13 ([PCINT23/AIN1]_PD7), JP5.6
GND: C1.2, C2.2, C3.2, C4.2, C5.2, IC1.8 (GND), IC1.22 (GND_1), IC2.2 (N.C._1), IC2.3 (N.C._2), IC2.5 (N.C._3), IC2.7 (GND), IC3.2 (N.C._1), IC3.3 (N.C._2), IC3.5 (N.C._3), IC3.7 (GND), IC4.7 (VSS), IC6.4 (V-), IC7.2 (N.C._1), IC7.3 (N.C._2), IC7.5 (N.C._3), IC7.7 (GND), ISP1.6 (GND), J1.6, JP1.3, JP4.3, R5.2, S1.1
MISO: IC1.18 (PB4_[MISO/PCINT4]), IC3.1 (COM), ISP1.1 (MISO)
MISO_OUT: IC3.8 (NC), JP7.2
MOSI: IC1.17 (PB3_[MOSI/OC2A/PCINT3]), IC4.4 (SDI), IC7.1 (COM), ISP1.4 (MOSI)
MOSI_OUT: IC7.8 (NC), JP7.1
MUX_COM: IC1.14 ([PCINT0/CLKO/ICP1]_PB0), IC6.3 (+IN), JP3.1
unnamed: C2.1, IC1.10 ([PCINT7/XTAL2/TOSC2]_PB7), Y1.1
unnamed: IC5.1 (OUT), R4.1
unnamed: IC2.6 (IN), IC3.6 (IN), IC7.6 (IN), S1.2
unnamed: IC5.2 (-IN), IC6.8 (V+), R4.2, R5.1
unnamed: IC1.15 (PB1_[OC1A/PCINT1]), IC4.5 (!LDAC)
unnamed: C1.1, IC1.9 ([PCINT6/XTAL1/TOSC1]_PB6), Y1.2
PC1: IC1.24 (PC1_[ADC1/PCINT9]), JP2.5
PC2: IC1.25 (PC2_[ADC2/PCINT10]), JP2.4
PC3: IC1.26 (PC3_[ADC3/PCINT11]), JP2.3
PC4: IC1.27 (PC4_[ADC4/SDA/PCINT12]), JP2.2
PC5: IC1.28 (PC5_[ADC5/SCL/PCINT13]), JP2.1
RESET: IC1.1 ([PCINT14/!RESET]_PC6), ISP1.5 (RST), R1.2
RX: IC1.2 ([PCINT16/RXD]_PD0), J1.3
SCK: IC1.19 (PB5_[SCK/PCINT5]), IC2.1 (COM), IC4.3 (SCK), ISP1.3 (SCK)
SCK_OUT: IC2.8 (NC), JP7.3
TX: IC1.3 ([PCINT17/TXD]_PD1), J1.2

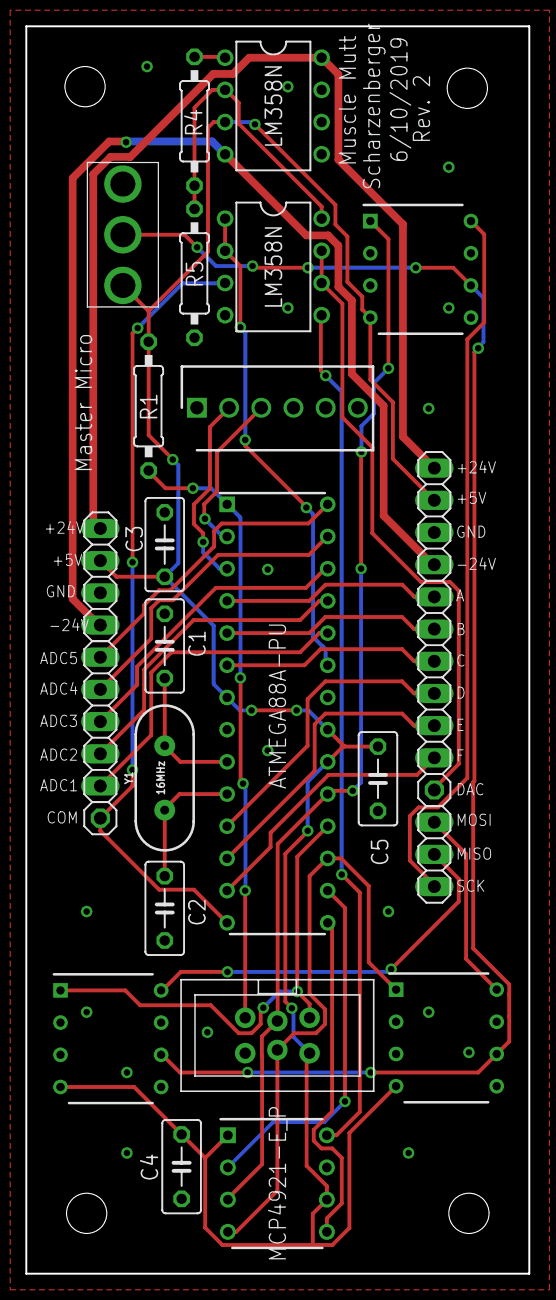
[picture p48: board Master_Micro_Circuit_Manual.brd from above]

Board: 2 copper layers, 39.7 x 98.4 mm, 26 parts (0 on the bottom side), 35 nets.

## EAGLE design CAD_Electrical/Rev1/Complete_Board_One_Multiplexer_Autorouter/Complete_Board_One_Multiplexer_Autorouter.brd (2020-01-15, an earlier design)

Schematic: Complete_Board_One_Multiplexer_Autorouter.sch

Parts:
C1, C2, C3, C13, C14, C15, C17, C20, C21, C22, C24, C27, C29, C32, C33, C34, C35, C36, C38, C41, C42, C43, C45, C48, C49, C50, C52, C55, C57, C60, C61, C62, C63, C64, C66, C69, C70, C71, C73, C76, C77, C78, C80, C83, C85, C88, C89, C90, C91, C92, C94, C97, C98, C99, C101, C104, C105, C106, C108, C111, C113, C116, C117, C118, C119, C120, C122, C125, C126, C127, C129, C132, C133, C134, C136, C139, C141, C144, C145, C146, C147, C148, C150, C153, C154, C155, C157, C160, C161, C162, C164, C167, C169, C172, C173, C174, C175, C176, C178, C181, C182, C183, C185, C188, C189, C190, C192, C195, C197, C200, C201, C202, C203, C204, C206, C209, C210, C211, C213, C216, C217, C218, C220, C223, C225, C228, C229, C230, C231, C232, C234, C237, C238, C239, C241, C244, C245, C246, C248, C251, C253, C256, C257, C258, C259, C260, C262, C265, C266, C267, C269, C272, C273, C274, C276, C279, C281, C284, C285, C286, C287, C288, C290, C293, C294, C296, C297, C299, C300, C302, C303, C305, C306, C308, C309, C311, C312, C314, C315, C317, C318, C320, C321, C323, C324, C326, C327, C329, C330, C332, C333, C335, C336, C338, C339, C341, C342, C344, C345, C347, C348, C350, C351, C353, C354, C356, C357, C359, C360, C362, C363: C-US050-030X075; C050-030X075
C4, C5, C7, C8, C10, C11, C18, C19, C25, C26, C30, C31, C39, C40, C46, C47, C53, C54, C58, C59, C67, C68, C74, C75, C81, C82, C86, C87, C95, C96, C102, C103, C109, C110, C114, C115, C123, C124, C130, C131, C137, C138, C142, C143, C151, C152, C158, C159, C165, C166, C170, C171, C179, C180, C186, C187, C193, C194, C198, C199, C207, C208, C214, C215, C221, C222, C226, C227, C235, C236, C242, C243, C249, C250, C254, C255, C263, C264, C270, C271, C277, C278, C282, C283, C291, C292: CPOL-USE2.5-7; E2,5-7
C6, C9, C12, C16, C23, C28, C37, C44, C51, C56, C65, C72, C79, C84, C93, C100, C107, C112, C121, C128, C135, C140, C149, C156, C163, C168, C177, C184, C191, C196, C205, C212, C219, C224, C233, C240, C247, C252, C261, C268, C275, C280, C289: CPOL-USE2.5-5; E2,5-5
IC1, IC86, IC88, IC90, IC92, IC94, IC96, IC98, IC100, IC102, IC104, IC106, IC108, IC110, IC112, IC114, IC116, IC118, IC120, IC122, IC124, IC126, IC128, IC130, IC132: ATMEGA88A-PU; DIP794W53P254L3467H457Q28N
IC2: MCP4921-E_P; DIP781W56P254L950H533Q8N
IC3, IC4: L78S24CV; TO270P460X1020X2008-3P
IC5: L7805CV; TO270P460X1020X2008-3P
IC6, IC7, IC8, IC9, IC10, IC11, IC12, IC13, IC14: CD4051BE; DIP254P762X508-16
IC15, IC16, IC17, IC18, IC19, IC20, IC21, IC22, IC23, IC24, IC25, IC26, IC27, IC28, IC29, IC30, IC31, IC32, IC33, IC34, IC35, IC36, IC37, IC38, IC39, IC40, IC41, IC42, IC43, IC44, IC45, IC46, IC47, IC48, IC49, IC50, IC51, IC52, IC53, IC54, IC55, IC56, IC57, IC58, IC59, IC60, IC61, IC62, IC63, IC64, IC65, IC66, IC67, IC68, IC69, IC70, IC71, IC72, IC73, IC74, IC75, IC76: LM324N; DIP794W56P254L1905H533Q14N
IC134, IC135, IC136: TBD62783APG; DIP762W55P254L2286H480Q18N
ISP1, ISP2, ISP3, ISP4, ISP5, ISP6, ISP7, ISP8, ISP9, ISP10, ISP11, ISP12, ISP13, ISP14, ISP15, ISP16, ISP17, ISP18, ISP19, ISP20, ISP21, ISP22, ISP23, ISP24, ISP25: AVRISP-BOX
J1, J2: CONN_025MM; SCREWTERMINAL-5MM-2
J3, J5: 30326-6002HB; SHDR26W81P254_2X13_4060X840X94
J4: 30316-6002HB; 3M-30316-6002HB
J6, J7, J8, J9, J10, J11, J12, J13, J14, J15, J16, J17, J18, J19, J20, J21, J22, J23, J24, J25, J26, J27, J28, J29, J30: 22-23-2061; SHDR6W87P0X254_1X6_1509X635X10
R1, R2, R3, R4, R5, R6, R7, R8, R9, R10, R11, R12, R13, R14, R15, R16, R17, R18, R19, R20, R21, R22, R23, R24, R25, R26, R27, R28, R29, R30, R31, R32, R33, R34, R35, R36, R37, R38, R39, R40, R41, R42, R43, R44, R45, R46, R47, R48, R49, R50, R51, R52, R53, R54, R55, R56, R57, R58, R59, R60, R61, R62, R63, R64, R65, R66, R67, R68, R69, R70, R71, R72, R73, R74, R75, R76, R77, R78, R79, R80, R81, R82, R83, R84, R85, R86, R87, R88, R89, R90, R91, R92, R93, R94, R95, R96, R97, R98, R99, R100, R101, R102, R103, R104, R105, R106, R107, R108, R109, R110, R111, R112, R113, R114, R115, R116, R117, R118, R119, R120, R121, R122, R123, R124, R125, R126, R127, R128, R129, R130, R131, R132, R133, R134, R135, R136, R137, R138, R139, R140, R141, R142, R143, R144, R145, R146, R147, R148, R149, R150, R151, R152, R153, R154, R155, R156, R157, R158, R159, R160, R161, R162, R163, R164, R165, R166, R167, R168, R169, R170, R171, R172, R173, R174, R175, R176, R177, R178, R179, R180, R181, R182, R183, R184, R185, R186, R187, R188, R189, R190, R191, R192, R193, R194, R195, R196, R197, R198, R199, R200, R201, R202, R203, R204, R205, R206, R207, R208, R209, R210, R211, R212, R213, R214, R215, R216, R217, R218, R219, R220, R221, R222, R223, R224, R225, R226, R227, R228, R229, R230, R231, R232, R233, R234, R235, R236, R237, R238, R239, R240, R241, R242, R243, R244, R245, R246, R247, R248, R249, R250, R251, R252, R253, R254, R255, R256, R257, R258, R259, R260, R261, R262, R263, R264, R265, R266, R267, R268, R269, R270, R271, R272, R273, R274, R275, R276, R277, R278, R279, R280, R281, R282, R283, R284, R285, R286, R287, R288, R289, R290, R291, R292, R293, R294, R295, R296, R297, R298, R299, R300, R301, R302, R303, R304, R305, R306, R307, R308, R309, R310, R311, R312, R313, R314, R315, R316, R317, R318, R319, R320, R321, R322, R323, R324, R325, R326, R327, R328, R329, R330, R331, R332, R333, R334, R335, R336, R337, R338, R339, R340, R341, R342, R343, R344, R345, R346, R347, R348, R349, R350, R351, R352, R353, R354, R355, R356, R357, R358, R359, R360, R361, R362, R363, R364, R365, R366, R367, R368, R369, R370, R371, R372, R373, R374, R375, R376, R377, R378, R379, R380, R381, R382, R383, R384, R385, R386, R387, R388, R389, R390, R391, R392, R393, R394, R395, R396, R397, R398, R399, R400, R401, R402, R403, R404, R405, R406, R407, R408, R409, R410, R411, R412, R413, R414, R415, R416, R417, R418, R419, R420, R421, R422, R423, R424, R425, R426, R427, R428, R429, R430, R431, R432, R433, R434, R435, R436, R437, R438, R439, R440, R441, R442, R443, R444, R445, R446, R447, R448, R449, R450, R451, R452, R453, R454, R455, R456, R457, R458, R459, R460, R461, R462, R463, R464, R465, R466, R467, R468, R469, R470, R471, R472, R473, R474, R475, R476, R477, R478, R479, R480, R481, R482, R483, R484, R485, R486, R487, R488, R489, R490, R491, R492, R493, R494, R495, R496, R497, R498, R499, R500, R501, R502, R503, R504, R505, R506, R507, R508, R509, R510, R511, R512, R513, R514, R515, R516, R517, R518, R519, R520, R521, R522, R523, R524, R525, R526, R527, R528, R529, R530, R531, R532, R533, R534, R535, R536, R537, R538, R539, R540, R541, R542, R543, R544, R545, R546, R547, R548, R549, R550, R551, R552, R553, R554, R555, R556, R557, R558, R559, R560, R561, R562, R563, R564, R565, R566, R567, R568, R569, R570, R571, R572, R573, R574, R575, R576, R577, R578, R579, R580, R581, R582, R583, R584, R585, R586, R587, R588, R589, R590, R591, R592, R593, R594, R595, R596, R597, R598, R599, R600, R601, R602, R603, R604, R605, R606, R607, R608, R609, R610, R611, R612, R613, R614, R615, R616, R617, R618, R619, R620, R621, R622, R623, R624, R625, R626, R627, R628, R629, R630, R631, R632, R633, R634, R635, R636, R637, R638, R639, R640, R641, R642, R643, R644, R645, R646, R647, R648, R649, R650, R651: R-US_0207/10; 0207/10
Y1, Y2, Y3, Y4, Y5, Y6, Y7, Y8, Y9, Y10, Y11, Y12, Y13, Y14, Y15, Y16, Y17, Y18, Y19, Y20, Y21, Y22, Y23, Y24, Y25: 16MHz; HC49US

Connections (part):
+5V: C3.1, C12.+, IC1.7 (VCC), IC1.20 (AVCC), IC1.21 (AREF), IC2.1 (VDD), IC2.6 (VREF), IC5.3 (OUTPUT), IC6.16 (VDD), IC7.16 (VDD), IC8.16 (VDD), IC9.16 (VDD), IC10.16 (VDD), IC11.16 (VDD), IC12.16 (VDD), IC13.16 (VDD), IC14.16 (VDD), IC16.5 (INPUT_2+), IC86.7 (VCC), IC86.20 (AVCC), IC86.21 (AREF), IC88.7 (VCC), IC88.20 (AVCC), IC88.21 (AREF), IC90.7 (VCC), IC90.20 (AVCC), IC90.21 (AREF), IC92.7 (VCC), IC92.20 (AVCC), IC92.21 (AREF), IC94.7 (VCC), IC94.20 (AVCC), IC94.21 (AREF), IC96.7 (VCC), IC96.20 (AVCC), IC96.21 (AREF), IC98.7 (VCC), IC98.20 (AVCC), IC98.21 (AREF), IC100.7 (VCC), IC100.20 (AVCC), IC100.21 (AREF), IC102.7 (VCC), IC102.20 (AVCC), IC102.21 (AREF), IC104.7 (VCC), IC104.20 (AVCC), IC104.21 (AREF), IC106.7 (VCC), IC106.20 (AVCC), IC106.21 (AREF), IC108.7 (VCC), IC108.20 (AVCC), IC108.21 (AREF), IC110.7 (VCC), IC110.20 (AVCC), IC110.21 (AREF), IC112.7 (VCC), IC112.20 (AVCC), IC112.21 (AREF), IC114.7 (VCC), IC114.20 (AVCC), IC114.21 (AREF), IC116.7 (VCC), IC116.20 (AVCC), IC116.21 (AREF), IC118.7 (VCC), IC118.20 (AVCC), IC118.21 (AREF), IC120.7 (VCC), IC120.20 (AVCC), IC120.21 (AREF), IC122.7 (VCC), IC122.20 (AVCC), IC122.21 (AREF), IC124.7 (VCC), IC124.20 (AVCC), IC124.21 (AREF), IC126.7 (VCC), IC126.20 (AVCC)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
+24V: C6.+, C10.+, C11.+, IC3.3 (OUT), IC5.1 (INPUT), IC16.4 (V+), IC17.4 (V+), IC18.4 (V+), IC19.4 (V+), IC20.4 (V+), IC21.4 (V+), IC22.4 (V+), IC23.4 (V+), IC24.4 (V+), IC25.4 (V+), IC26.4 (V+), IC27.4 (V+), IC28.4 (V+), IC29.4 (V+), IC30.4 (V+), IC31.4 (V+), IC32.4 (V+), IC33.4 (V+), IC34.4 (V+), IC35.4 (V+), IC36.4 (V+), IC37.4 (V+), IC38.4 (V+), IC39.4 (V+), IC40.4 (V+), IC41.4 (V+), IC42.4 (V+), IC43.4 (V+), IC44.4 (V+), IC45.4 (V+), IC46.4 (V+), IC47.4 (V+), IC48.4 (V+), IC49.4 (V+), IC50.4 (V+), IC51.4 (V+), IC52.4 (V+), IC53.4 (V+), IC54.4 (V+), IC55.4 (V+), IC56.4 (V+), IC57.4 (V+), IC58.4 (V+), IC59.4 (V+), IC60.4 (V+), IC61.4 (V+), IC62.4 (V+), IC63.4 (V+), IC64.4 (V+), IC65.4 (V+), IC66.4 (V+), IC67.4 (V+), IC68.4 (V+), IC69.4 (V+), IC70.4 (V+), IC71.4 (V+), IC72.4 (V+), IC73.4 (V+), IC74.4 (V+), IC75.4 (V+), IC76.4 (V+), IC134.9 (VCC), IC135.9 (VCC), IC136.9 (VCC), J4.1
-24V: C7.-, C8.-, C9.-, IC4.2 (GND), IC16.11 (GND), IC17.11 (GND), IC18.11 (GND), IC19.11 (GND), IC20.11 (GND), IC21.11 (GND), IC22.11 (GND), IC23.11 (GND), IC24.11 (GND), IC25.11 (GND), IC26.11 (GND), IC27.11 (GND), IC28.11 (GND), IC29.11 (GND), IC30.11 (GND), IC31.11 (GND), IC32.11 (GND), IC33.11 (GND), IC34.11 (GND), IC35.11 (GND), IC36.11 (GND), IC37.11 (GND), IC38.11 (GND), IC39.11 (GND), IC40.11 (GND), IC41.11 (GND), IC42.11 (GND), IC43.11 (GND), IC44.11 (GND), IC45.11 (GND), IC46.11 (GND), IC47.11 (GND), IC48.11 (GND), IC49.11 (GND), IC50.11 (GND), IC51.11 (GND), IC52.11 (GND), IC53.11 (GND), IC54.11 (GND), IC55.11 (GND), IC56.11 (GND), IC57.11 (GND), IC58.11 (GND), IC59.11 (GND), IC60.11 (GND), IC61.11 (GND), IC62.11 (GND), IC63.11 (GND), IC64.11 (GND), IC65.11 (GND), IC66.11 (GND), IC67.11 (GND), IC68.11 (GND), IC69.11 (GND), IC70.11 (GND), IC71.11 (GND), IC72.11 (GND), IC73.11 (GND), IC74.11 (GND), IC75.11 (GND), IC76.11 (GND), J2.1
A0: IC1.4 ([PCINT18/INT0]_PD2), IC6.11 (A)
ADC00: IC1.23 (PC0_[ADC0/PCINT8]), IC15.6 (INPUT_2-), IC15.7 (OUTPUT_2)
B0: IC1.5 ([PCINT19/OC2B/INT1]_PD3), IC6.10 (B)
C0: IC1.6 ([PCINT20/XCK/T0]_PD4), IC6.9 (C)
D0: IC1.11 ([PCINT21/OC0B/T1]_PD5), IC7.11 (A), IC8.11 (A), IC9.11 (A), IC10.11 (A), IC11.11 (A), IC12.11 (A), IC13.11 (A), IC14.11 (A)
DAC00: IC2.8 (VOUT), IC15.10 (INPUT_3+)
DEMUXIN: IC15.8 (OUTPUT_3), IC15.9 (INPUT_3-)
E0: IC1.12 ([PCINT22/OC0A/AIN0]_PD6), IC7.10 (B), IC8.10 (B), IC9.10 (B), IC10.10 (B), IC11.10 (B), IC12.10 (B), IC13.10 (B), IC14.10 (B)
F0: IC1.13 ([PCINT23/AIN1]_PD7), IC7.9 (C), IC8.9 (C), IC9.9 (C), IC10.9 (C), IC11.9 (C), IC12.9 (C), IC13.9 (C), IC14.9 (C)
FOUT00: C17.1, IC17.12 (INPUT_4+), IC47.7 (OUTPUT_2), R251.1
FOUT01: C29.1, IC17.10 (INPUT_3+), IC48.8 (OUTPUT_3), R266.2
FOUT02: C24.1, IC19.3 (INPUT_1+), IC48.7 (OUTPUT_2), R260.1
FOUT03: C38.1, IC19.5 (INPUT_2+), IC49.8 (OUTPUT_3), R278.2
FOUT04: C45.1, IC20.12 (INPUT_4+), IC50.7 (OUTPUT_2), R287.1
FOUT05: C57.1, IC20.10 (INPUT_3+), IC51.8 (OUTPUT_3), R302.2
FOUT06: C52.1, IC22.3 (INPUT_1+), IC51.7 (OUTPUT_2), R296.1
FOUT07: C66.1, IC22.5 (INPUT_2+), IC52.8 (OUTPUT_3), R314.2
FOUT08: C73.1, IC23.12 (INPUT_4+), IC53.7 (OUTPUT_2), R323.1
FOUT09: C85.1, IC23.10 (INPUT_3+), IC54.8 (OUTPUT_3), R338.2
FOUT10: C80.1, IC25.3 (INPUT_1+), IC54.7 (OUTPUT_2), R332.1
FOUT11: C94.1, IC25.5 (INPUT_2+), IC55.8 (OUTPUT_3), R350.2
FOUT12: C101.1, IC26.12 (INPUT_4+), IC56.7 (OUTPUT_2), R359.1
FOUT13: C113.1, IC26.10 (INPUT_3+), IC57.8 (OUTPUT_3), R374.2
FOUT14: C108.1, IC28.3 (INPUT_1+), IC57.7 (OUTPUT_2), R368.1
FOUT15: C122.1, IC28.5 (INPUT_2+), IC58.8 (OUTPUT_3), R386.2
FOUT16: C129.1, IC29.12 (INPUT_4+), IC59.7 (OUTPUT_2), R395.1
FOUT17: C141.1, IC29.10 (INPUT_3+), IC60.8 (OUTPUT_3), R410.2
FOUT18: C136.1, IC31.3 (INPUT_1+), IC60.7 (OUTPUT_2), R404.1
FOUT19: C150.1, IC31.5 (INPUT_2+), IC61.8 (OUTPUT_3), R422.2
FOUT20: C157.1, IC32.12 (INPUT_4+), IC62.7 (OUTPUT_2), R431.1
FOUT21: C169.1, IC32.10 (INPUT_3+), IC63.8 (OUTPUT_3), R446.2
FOUT22: C164.1, IC34.3 (INPUT_1+), IC63.7 (OUTPUT_2), R440.1
FOUT23: C178.1, IC34.5 (INPUT_2+), IC64.8 (OUTPUT_3), R458.2
FOUT24: C185.1, IC35.12 (INPUT_4+), IC65.7 (OUTPUT_2), R467.1
FOUT25: C197.1, IC35.10 (INPUT_3+), IC66.8 (OUTPUT_3), R482.2
FOUT26: C192.1, IC37.3 (INPUT_1+), IC66.7 (OUTPUT_2), R476.1
FOUT27: C206.1, IC37.5 (INPUT_2+), IC67.8 (OUTPUT_3), R494.2
FOUT28: C213.1, IC38.12 (INPUT_4+), IC68.7 (OUTPUT_2), R503.1
FOUT29: C225.1, IC38.10 (INPUT_3+), IC69.8 (OUTPUT_3), R518.2
FOUT30: C220.1, IC40.3 (INPUT_1+), IC69.7 (OUTPUT_2), R512.1
FOUT31: C234.1, IC40.5 (INPUT_2+), IC70.8 (OUTPUT_3), R530.2
FOUT32: C241.1, IC41.12 (INPUT_4+), IC71.7 (OUTPUT_2), R539.1
FOUT33: C253.1, IC41.10 (INPUT_3+), IC72.8 (OUTPUT_3), R554.2
FOUT34: C248.1, IC43.3 (INPUT_1+), IC72.7 (OUTPUT_2), R548.1
FOUT35: C262.1, IC43.5 (INPUT_2+), IC73.8 (OUTPUT_3), R566.2
FOUT36: C269.1, IC44.12 (INPUT_4+), IC74.7 (OUTPUT_2), R575.1
FOUT37: C281.1, IC44.10 (INPUT_3+), IC75.8 (OUTPUT_3), R590.2
FOUT38: C276.1, IC46.3 (INPUT_1+), IC75.7 (OUTPUT_2), R584.1
FOUT39: C290.1, IC46.5 (INPUT_2+), IC76.8 (OUTPUT_3), R602.2
GND: C1.2, C2.2, C3.2, C4.-, C5.-, C6.-, C9.+, C10.-, C11.-, C12.-, C14.2, C16.-, C18.-, C19.-, C21.2, C23.-, C25.-, C26.-, C28.-, C30.-, C31.-, C33.2, C35.2, C37.-, C39.-, C40.-, C42.2, C44.-, C46.-, C47.-, C49.2, C51.-, C53.-, C54.-, C56.-, C58.-, C59.-, C61.2, C63.2, C65.-, C67.-, C68.-, C70.2, C72.-, C74.-, C75.-, C77.2, C79.-, C81.-, C82.-, C84.-, C86.-, C87.-, C89.2, C91.2, C93.-, C95.-, C96.-, C98.2, C100.-, C102.-, C103.-, C105.2, C107.-, C109.-, C110.-, C112.-, C114.-, C115.-, C117.2, C119.2, C121.-, C123.-, C124.-, C126.2, C128.-, C130.-, C131.-, C133.2, C135.-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
MISO00: IC1.18 (PB4_[MISO/PCINT4]), ISP1.1 (MISO)
MISO01: IC86.18 (PB4_[MISO/PCINT4]), ISP2.1 (MISO)
MISO02: IC88.18 (PB4_[MISO/PCINT4]), ISP3.1 (MISO)
MISO03: IC90.18 (PB4_[MISO/PCINT4]), ISP4.1 (MISO)
MISO04: IC92.18 (PB4_[MISO/PCINT4]), ISP5.1 (MISO)
MISO05: IC94.18 (PB4_[MISO/PCINT4]), ISP6.1 (MISO)
MISO06: IC96.18 (PB4_[MISO/PCINT4]), ISP7.1 (MISO)
MISO07: IC98.18 (PB4_[MISO/PCINT4]), ISP8.1 (MISO)
MISO08: IC100.18 (PB4_[MISO/PCINT4]), ISP9.1 (MISO)
MISO09: IC102.18 (PB4_[MISO/PCINT4]), ISP10.1 (MISO)
MISO10: IC104.18 (PB4_[MISO/PCINT4]), ISP11.1 (MISO)
MISO11: IC106.18 (PB4_[MISO/PCINT4]), ISP12.1 (MISO)
MISO12: IC108.18 (PB4_[MISO/PCINT4]), ISP13.1 (MISO)
MISO13: IC110.18 (PB4_[MISO/PCINT4]), ISP14.1 (MISO)
MISO14: IC112.18 (PB4_[MISO/PCINT4]), ISP15.1 (MISO)
MISO15: IC114.18 (PB4_[MISO/PCINT4]), ISP16.1 (MISO)
MISO16: IC116.18 (PB4_[MISO/PCINT4]), ISP17.1 (MISO)
MISO17: IC118.18 (PB4_[MISO/PCINT4]), ISP18.1 (MISO)
MISO18: IC120.18 (PB4_[MISO/PCINT4]), ISP19.1 (MISO)
MISO19: IC122.18 (PB4_[MISO/PCINT4]), ISP20.1 (MISO)
MISO20: IC124.18 (PB4_[MISO/PCINT4]), ISP21.1 (MISO)
MISO21: IC126.18 (PB4_[MISO/PCINT4]), ISP22.1 (MISO)
MISO22: IC128.18 (PB4_[MISO/PCINT4]), ISP23.1 (MISO)
MISO23: IC130.18 (PB4_[MISO/PCINT4]), ISP24.1 (MISO)
MISO24: IC132.18 (PB4_[MISO/PCINT4]), ISP25.1 (MISO)
MOSI00: IC1.17 (PB3_[MOSI/OC2A/PCINT3]), IC2.4 (SDI), IC86.17 (PB3_[MOSI/OC2A/PCINT3]), IC88.17 (PB3_[MOSI/OC2A/PCINT3]), IC90.17 (PB3_[MOSI/OC2A/PCINT3]), IC92.17 (PB3_[MOSI/OC2A/PCINT3]), IC94.17 (PB3_[MOSI/OC2A/PCINT3]), IC96.17 (PB3_[MOSI/OC2A/PCINT3]), IC98.17 (PB3_[MOSI/OC2A/PCINT3]), IC100.17 (PB3_[MOSI/OC2A/PCINT3]), IC102.17 (PB3_[MOSI/OC2A/PCINT3]), IC104.17 (PB3_[MOSI/OC2A/PCINT3]), IC106.17 (PB3_[MOSI/OC2A/PCINT3]), IC108.17 (PB3_[MOSI/OC2A/PCINT3]), IC110.17 (PB3_[MOSI/OC2A/PCINT3]), IC112.17 (PB3_[MOSI/OC2A/PCINT3]), IC114.17 (PB3_[MOSI/OC2A/PCINT3]), IC116.17 (PB3_[MOSI/OC2A/PCINT3]), IC118.17 (PB3_[MOSI/OC2A/PCINT3]), IC120.17 (PB3_[MOSI/OC2A/PCINT3]), IC122.17 (PB3_[MOSI/OC2A/PCINT3]), IC124.17 (PB3_[MOSI/OC2A/PCINT3]), IC126.17 (PB3_[MOSI/OC2A/PCINT3]), IC128.17 (PB3_[MOSI/OC2A/PCINT3]), IC130.17 (PB3_[MOSI/OC2A/PCINT3]), IC132.17 (PB3_[MOSI/OC2A/PCINT3]), ISP1.4 (MOSI), ISP2.4 (MOSI), ISP3.4 (MOSI), ISP4.4 (MOSI), ISP5.4 (MOSI), ISP6.4 (MOSI), ISP7.4 (MOSI), ISP8.4 (MOSI), ISP9.4 (MOSI), ISP10.4 (MOSI), ISP11.4 (MOSI), ISP12.4 (MOSI), ISP13.4 (MOSI), ISP14.4 (MOSI), ISP15.4 (MOSI), ISP16.4 (MOSI), ISP17.4 (MOSI), ISP18.4 (MOSI), ISP19.4 (MOSI), ISP20.4 (MOSI), ISP21.4 (MOSI), ISP22.4 (MOSI), ISP23.4 (MOSI), ISP24.4 (MOSI), ISP25.4 (MOSI)
MUX00: IC7.13 (CHANNELS_IN/OUT_0), IC17.1 (OUTPUT_1), IC86.23 (PC0_[ADC0/PCINT8]), IC88.24 (PC1_[ADC1/PCINT9]), R9.1
MUX01: IC7.14 (CHANNELS_IN/OUT_1), IC18.14 (OUTPUT_4), IC86.24 (PC1_[ADC1/PCINT9]), IC88.23 (PC0_[ADC0/PCINT8]), R21.1
MUX02: IC7.15 (CHANNELS_IN/OUT_2), IC18.1 (OUTPUT_1), IC90.23 (PC0_[ADC0/PCINT8]), IC92.24 (PC1_[ADC1/PCINT9]), R15.1
MUX03: IC7.12 (CHANNELS_IN/OUT_3), IC19.14 (OUTPUT_4), IC90.24 (PC1_[ADC1/PCINT9]), IC92.23 (PC0_[ADC0/PCINT8]), R27.1
MUX04: IC7.1 (CHANNELS_IN/OUT_4), IC20.1 (OUTPUT_1), IC94.23 (PC0_[ADC0/PCINT8]), IC96.24 (PC1_[ADC1/PCINT9]), R33.1
MUX05: IC7.5 (CHANNELS_IN/OUT_5), IC21.14 (OUTPUT_4), IC94.24 (PC1_[ADC1/PCINT9]), IC96.23 (PC0_[ADC0/PCINT8]), R45.1
MUX06: IC7.2 (CHANNELS_IN/OUT_6), IC21.1 (OUTPUT_1), IC98.23 (PC0_[ADC0/PCINT8]), IC100.24 (PC1_[ADC1/PCINT9]), R39.1
MUX07: IC7.4 (CHANNELS_IN/OUT_7), IC22.14 (OUTPUT_4), IC98.24 (PC1_[ADC1/PCINT9]), IC100.23 (PC0_[ADC0/PCINT8]), R50.1
MUX08: IC8.13 (CHANNELS_IN/OUT_0), IC23.1 (OUTPUT_1), IC102.23 (PC0_[ADC0/PCINT8]), IC104.24 (PC1_[ADC1/PCINT9]), R57.1
MUX09: IC8.14 (CHANNELS_IN/OUT_1), IC24.14 (OUTPUT_4), IC102.24 (PC1_[ADC1/PCINT9]), IC104.23 (PC0_[ADC0/PCINT8]), R69.1
MUX10: IC8.15 (CHANNELS_IN/OUT_2), IC24.1 (OUTPUT_1), IC106.23 (PC0_[ADC0/PCINT8]), IC108.24 (PC1_[ADC1/PCINT9]), R63.1
MUX11: IC8.12 (CHANNELS_IN/OUT_3), IC25.14 (OUTPUT_4), IC106.24 (PC1_[ADC1/PCINT9]), IC108.23 (PC0_[ADC0/PCINT8]), R74.1
MUX12: IC8.1 (CHANNELS_IN/OUT_4), IC26.1 (OUTPUT_1), IC110.23 (PC0_[ADC0/PCINT8]), IC112.24 (PC1_[ADC1/PCINT9]), R81.1
MUX13: IC8.5 (CHANNELS_IN/OUT_5), IC27.14 (OUTPUT_4), IC110.24 (PC1_[ADC1/PCINT9]), IC112.23 (PC0_[ADC0/PCINT8]), R93.1
MUX14: IC8.2 (CHANNELS_IN/OUT_6), IC27.1 (OUTPUT_1), IC114.23 (PC0_[ADC0/PCINT8]), IC116.24 (PC1_[ADC1/PCINT9]), R87.1
MUX15: IC8.4 (CHANNELS_IN/OUT_7), IC28.14 (OUTPUT_4), IC114.24 (PC1_[ADC1/PCINT9]), IC116.23 (PC0_[ADC0/PCINT8]), R98.1
MUX16: IC9.13 (CHANNELS_IN/OUT_0), IC29.1 (OUTPUT_1), IC118.23 (PC0_[ADC0/PCINT8]), IC120.24 (PC1_[ADC1/PCINT9]), R105.1
MUX17: IC9.14 (CHANNELS_IN/OUT_1), IC30.14 (OUTPUT_4), IC118.24 (PC1_[ADC1/PCINT9]), IC120.23 (PC0_[ADC0/PCINT8]), R117.1
MUX18: IC9.15 (CHANNELS_IN/OUT_2), IC30.1 (OUTPUT_1), IC122.23 (PC0_[ADC0/PCINT8]), IC124.24 (PC1_[ADC1/PCINT9]), R111.1
MUX19: IC9.12 (CHANNELS_IN/OUT_3), IC31.14 (OUTPUT_4), IC122.24 (PC1_[ADC1/PCINT9]), IC124.23 (PC0_[ADC0/PCINT8]), R122.1
MUX20: IC9.1 (CHANNELS_IN/OUT_4), IC32.1 (OUTPUT_1), IC126.23 (PC0_[ADC0/PCINT8]), IC128.24 (PC1_[ADC1/PCINT9]), R129.1
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

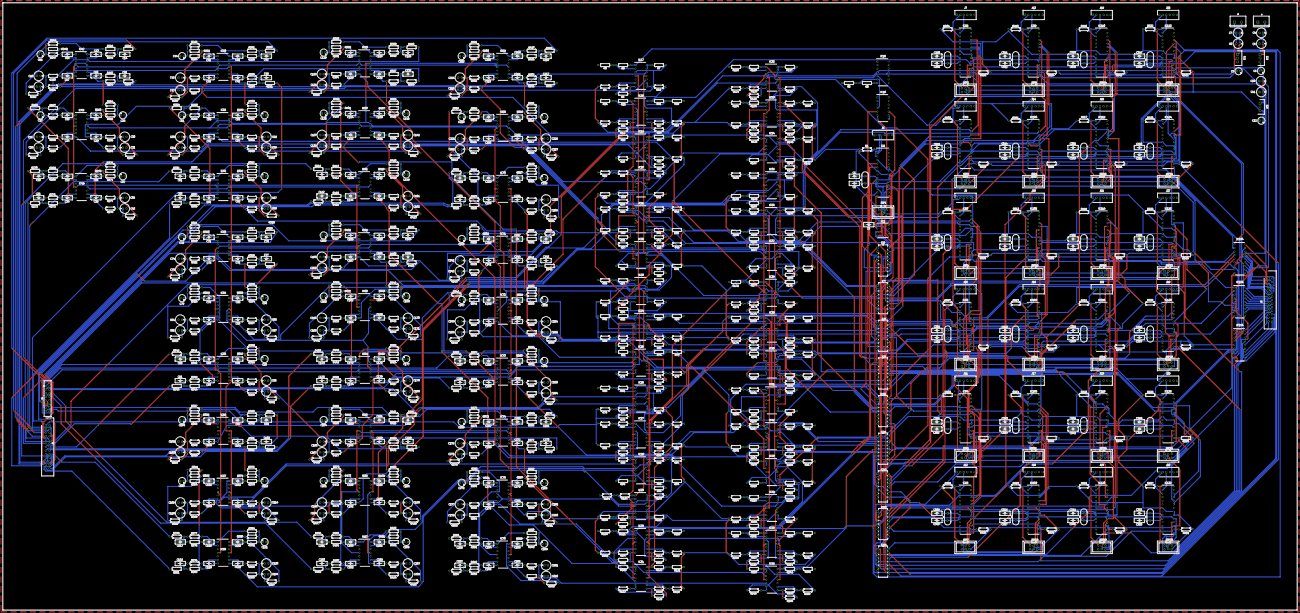
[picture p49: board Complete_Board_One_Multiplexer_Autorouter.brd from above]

Board: 2 copper layers, 916.9 x 430.2 mm, 1174 parts (0 on the bottom side), 890 nets.

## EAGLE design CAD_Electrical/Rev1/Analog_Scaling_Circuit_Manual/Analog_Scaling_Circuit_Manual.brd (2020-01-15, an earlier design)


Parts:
IC1, IC2, IC3: LM324N; DIP794W56P254L1905H533Q14N
JP1, JP2, JP3, JP4: PINHD-1X4; 1X04
R1, R2, R5, R7, R17, R19, R21, R24: 3.3 kO; 0207/10
R3, R4, R9, R11, R13, R15, R22, R23: 4.7 kO; 0207/10
R6, R8, R18, R20: 33 kO; 0207/10
R10, R12, R14, R16: 5.6 kO; 0207/10

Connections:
+5V: JP2.3, JP3.2, R6.2, R8.2, R18.1, R20.1
+24V: IC1.4 (V+), IC2.4 (V+), IC3.4 (V+), JP2.4, JP3.1
-24V: IC1.11 (GND), IC2.11 (GND), IC3.11 (GND), JP2.1, JP3.4
GND: IC1.5 (INPUT_2+), IC2.5 (INPUT_2+), IC2.10 (INPUT_3+), IC3.10 (INPUT_3+), JP2.2, JP3.3, R5.2, R7.2, R17.2, R19.2
IN0: IC1.12 (INPUT_4+), JP4.4
IN1: IC1.10 (INPUT_3+), JP4.3
IN2: IC3.3 (INPUT_1+), JP4.2
IN3: IC3.5 (INPUT_2+), JP4.1
unnamed: IC1.13 (INPUT_4-), IC1.14 (OUTPUT_4), R2.2
unnamed: IC1.6 (INPUT_2-), R6.1, R10.1
unnamed: IC1.7 (OUTPUT_2), R3.1, R10.2
unnamed: IC1.3 (INPUT_1+), R2.1, R3.2
unnamed: IC1.2 (INPUT_1-), R5.1, R9.2
unnamed: IC2.6 (INPUT_2-), R8.1, R12.1
unnamed: IC2.7 (OUTPUT_2), R4.1, R12.2
unnamed: IC2.3 (INPUT_1+), R1.1, R4.2
unnamed: IC2.2 (INPUT_1-), R7.1, R11.2
unnamed: IC1.8 (OUTPUT_3), IC1.9 (INPUT_3-), R21.2
unnamed: IC2.13 (INPUT_4-), R13.2, R17.1
unnamed: IC3.1 (OUTPUT_1), IC3.2 (INPUT_1-), R1.2
unnamed: IC2.12 (INPUT_4+), R21.1, R22.2
unnamed: IC2.9 (INPUT_3-), R14.2, R18.2
unnamed: IC2.8 (OUTPUT_3), R14.1, R22.1
unnamed: IC3.13 (INPUT_4-), R15.2, R19.1
unnamed: IC3.12 (INPUT_4+), R23.2, R24.2
unnamed: IC3.9 (INPUT_3-), R16.2, R20.2
unnamed: IC3.8 (OUTPUT_3), R16.1, R23.1
unnamed: IC3.6 (INPUT_2-), IC3.7 (OUTPUT_2), R24.1
OUT0: IC1.1 (OUTPUT_1), JP1.1, R9.1
OUT1: IC2.14 (OUTPUT_4), JP1.2, R13.1
OUT2: IC2.1 (OUTPUT_1), JP1.3, R11.1
OUT3: IC3.14 (OUTPUT_4), JP1.4, R15.1


Board: 2 copper layers, 74.6 x 92.1 mm, 31 parts (0 on the bottom side), 32 nets.

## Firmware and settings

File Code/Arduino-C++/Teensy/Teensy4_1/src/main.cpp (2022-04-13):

#include <Arduino.h>
#include <Encoder.h>

//Create Objects
Encoder encoder1(2,3);
Encoder encoder2(4,5);
Encoder encoder3(6,7);

//Declare Variables
unsigned long previousTime = millis();
unsigned long timeInterval = 1; //1 ms
unsigned long previousTime1 = millis();
unsigned long timeInterval1 = 500; //.25 

int pressureSensor1 = 14;
int pressureSensor2 = 15;
int pressureSensor3 = 20;
int pressureSensor4 = 21;
int pressureSensor5 = 22;
int pressureSensor6 = 23;

int pressureReading1;
int pressureReading2;
int pressureReading3;
int pressureReading4;
int pressureReading5;
int pressureReading6;

double positionEncoder1 = -999.0;
double positionEncoder2 = -999.0;
double positionEncoder3 = -999.0;

void setup() {
  Serial.begin(115200);
  
  pinMode(32, OUTPUT); //Hip 1
  pinMode(33, OUTPUT); //Hip 2
  pinMode(34, OUTPUT); //Ankle 1
  pinMode(35, OUTPUT); //Knee 1
  pinMode(36, OUTPUT); //Ankle 2
  pinMode(37, OUTPUT); //Knee 2
}

void loop() {

  //Read Keyboard Input
  if(Serial.available()) {
    char input1 = Serial.read();
    if(input1 == '1') {
      digitalWrite(32, HIGH);
    }

    else if(input1 == '0') {
      digitalWrite(32,LOW);
    }
  }

  //Read Pressure Sensors
  unsigned long currentTime = millis();

  if (currentTime - previousTime >= timeInterval) {
    pressureReading1  = 0.797*analogRead(pressureSensor1)-127;
    pressureReading2  = 0.797*analogRead(pressureSensor2)-127;
    pressureReading3  = 0.797*analogRead(pressureSensor3)-127;
    pressureReading4  = 0.797*analogRead(pressureSensor4)-127;
    pressureReading5  = 0.797*analogRead(pressureSensor5)-127;
    pressureReading6  = 0.797*analogRead(pressureSensor6)-127;
    previousTime = currentTime;
  }

  //Print Pressure Sensor Data
  if (currentTime - previousTime1 >= timeInterval1) {
    Serial.print("Sensor 1:  ");
    Serial.print(pressureReading1);
    Serial.print("\t");
    Serial.print("Sensor 2:  ");
    Serial.print(pressureReading2);
    Serial.print("\t");
    Serial.print("Sensor 3:  ");
    Serial.print(pressureReading3);
    Serial.print("\t");
    Serial.print("Sensor 4:  ");
    Serial.print(pressureReading4);
    Serial.print("\t");
    Serial.print("Sensor 5:  ");
    Serial.print(pressureReading5);
    Serial.print("\t");
    Serial.print("Sensor 6:  ");
    Serial.print(pressureReading6);
    Serial.println();
    
    previousTime1 = currentTime;
  }

  // Reading Encoders
  double newEncoder1;
  double newEncoder2;
  double newEncoder3;

  newEncoder1 = encoder1.read()*0.04395; //Hip position in degrees
  newEncoder2 = encoder2.read()*0.04395; //Ankle position in degrees
  newEncoder3 = encoder3.read()*0.04395; //Knee position in degrees

  if (newEncoder1 != positionEncoder1) {
    positionEncoder1 = newEncoder1;
  }
   if (newEncoder2 != positionEncoder2) {
    positionEncoder2 = newEncoder2;
  } 
  if (newEncoder3 != positionEncoder3) {
    positionEncoder3 = newEncoder3;
  }

  if (currentTime - previousTime1 >= timeInterval1) 
  {
    Serial.print("Hip Angle = ");
    Serial.print(positionEncoder1);
    Serial.print("\t");
    Serial.print("\t");
    Serial.print("Knee Angle = ");
    Serial.print(positionEncoder3);
    Serial.print("\t");
    Serial.print("\t");
    Serial.print("Ankle Angle = ");
    Serial.print(positionEncoder2);
    Serial.println();
    previousTime1 = currentTime;
  }

}

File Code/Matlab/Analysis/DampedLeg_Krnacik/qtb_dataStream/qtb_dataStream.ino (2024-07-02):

/* qtb_dataStream.ino
 * 
 * This sketch generates a data stream based on readings taken from encoders 
 * mounted to the Quadruped Test Bench in the Agile & Adaptive Robotics 
 * Laboratory at Portland State University. 
 * 
 * User-board communications are enabled via the serial window with limited
 * ability to control key variables. Parseable serial inputs are:
 * 'p': toggles message display (1) 
 * 'v': toggles message verbosity (2)
 * 'a': tares ankle encoder
 * 'h': tares hip encoder
 * 'k': tares knee encoder
 * 's': toggles averaging strategy (3). [1] -> [2] -> [0] -> [1] -> ...
 * 
 * Notes:
 * (1) Effectively serves as a pause function for the displayed data stream
 * 
 * (2) Verbose messages include language to inform the reader of both the 
 * encoder and the value. A fourth column reports the time modulus 
 * (reference = 1000 ms). Non-verbose messages contain only the encoder 
 * values and the time. 
 * 
 * (3) Because the encoders are inherently noisy, averaging strategies are 
 * often useful for data collection efforts. Here the user can choose from 
 * raw values (avg_strategy = 0), a simple averaging strategy (avg_strategy
 * = 1), or an exponentially-weighted average (avg_strategy = 2) with a gain
 * variable (beta, see "user-controlled variables" below) that can be tuned 
 * to balance response speed with signal stability. The number of readings 
 * across which to average is controlled by the variable n below.
 * 
 * Written by Stu McNeal
 * 10/5/2022
 */

#include <Arduino.h>
#include <Encoder.h>

// **********************************************************************
// user-controlled variables
// ----------------------------------------------------------------------

//--time controls
unsigned int timeInterval = 10; // [ms] time between readings printed

//--averaging controls
int avg_strategy  = 2   ;//0: none (noisy); 1: standard averaging; 2: exponential (ie weighted) averaging (most stable)

float beta        = 0.15;//gain variable representing weight of new reading. (must be 0 < beta < 1)
int n             = 20  ;//[#] number of readings across which to average

//--display settings
bool displayMsg   = true;//determines whether to print angles to serial window
bool verboseMsg   = false;//determines whether context is printed with joint angles

// **********************************************************************

// define i/o pin locations (included here for system ID purposes)
#define Hip1 32   // Hip 1 
#define Hip2 33   // Hip 2
#define Ankle1 34 // Ankle 1
#define Ankle2 36 // Ankle 2
#define Knee1 35  // Knee 1
#define Knee2 37  // Knee 2

// create encoder objects
Encoder encoderHip(2,3);
Encoder encoderAnk(4,5);
Encoder encoderKne(6,7);

// initialize joint position vars
double positionHip   = -999.0;
double positionKnee  = -999.0;
double positionAnkle = -999.0;

// initialize joint position vars for averaging
double angleHip = 0;
double angleKne = 0;
double angleAnk = 0;

// initialize time vars
unsigned long previousTime = millis();

// ******************** setup() ****************************************
void setup(){
  // initialize serial communications
  Serial.begin(57600);
}

// ******************** loop() *****************************************
void loop(){
  // once timeInterval has passed, fetch current joint angles
  if(millis() - previousTime >= timeInterval)
  {
    //update encoder readings
    updateJointAngles();
    
    //if specified, print joint angles to serial monitor
    if(displayMsg){printMsg();}
    
    //reset the timer
    previousTime = millis();
  }

  // Serial Interfacing
  if(Serial.available()) {
    char msg = Serial.read();
    if (msg != '\n'){
    parseMsg(msg);
    }
    Serial.flush();
  }
} 

// ******************** parseMsg(msg) **********************************
void parseMsg(char msg){ 
  /* parseMsg(msg) receives the character sent by the user to the serial 
   * window and toggles the corresponding control, described below. parseMsg(msg) returns nothing.
   * 
   * parseMsg interprets the following serial inputs:
   * 'p': toggles message display (ie pause the data stream)
   * 'v': toggles message verbosity
   * 'a': tares ankle encoder
   * 'h': tares hip encoder
   * 'k': tares knee encoder
   * 's': toggles averaging strategy. [0] -> [1] -> [2] -> [0] -> [1] -> ...
   */

   
  // turn on the muscle of interest
  if(msg == 'p'){
    displayMsg = !displayMsg;//toggle print messages
  } else if(msg == 'v'){
    verboseMsg = !verboseMsg;//toggle message verbosity
  } else if(msg == 'a'){
    encoderAnk.write(0);//tare ankle encoder
  } else if(msg == 'h'){
    encoderHip.write(0);//tare hip encoder
  } else if(msg == 'k'){
    encoderKne.write(0);//tare knee encoder
  } else if(msg == 's'){
    avg_strategy = (avg_strategy + 1) % 3;//toggle averaging strategy

    // notify user of current setting and pause for 3/4 seconds
    Serial.print("Averaging strategy = ");
    Serial.println(avg_strategy);
    delay(750);
  } else{
    Serial.println("no matches");
  }
}

// ******************** updateJointAngles() ****************************
void updateJointAngles(){
  /* This function updates encoder readings according to the averaging 
  * strategy determined by the avg_strategy variable. If 
  * displayMsg==true, the function calls printEncoders(). Returns 
  * nothing.
  *
  * The averaging strategies, based on avg_strategy, are: 
  * avg_strategy == 0: no averaging applied, raw value printed 
  * avg_strategy == 1: simple averaging applied
  * avg_strategy == 2: exponentially-weighted averaging applied
  */
  
  // Case 0: raw values, no averaging applied:
  if (avg_strategy == 0){
    angleHip += encoderHip.read()*0.04395;
    angleKne += encoderKne.read()*0.04395;
    angleAnk += encoderAnk.read()*0.04395;
  } else {
    
    // generate vars to hold the current average sensor value
    float tempAvgHip=0, tempAvgKne=0, tempAvgAnk=0;
  
    // calculate the current sensor average (in degrees)
    for (int i=0;i<n;i++){
      tempAvgHip += encoderHip.read()*0.04395;
      tempAvgKne += encoderKne.read()*0.04395;
      tempAvgAnk += encoderAnk.read()*0.04395;
    }
    tempAvgHip /= n;  tempAvgKne /= n; tempAvgAnk /= n;

    // Case 1: normal averaging
    if (avg_strategy == 1){
      
      // update encoder vars using simple averaging
      angleHip = tempAvgHip; angleKne = tempAvgKne; angleAnk = tempAvgAnk;

    // Case 2: exponentially weighted averaging  
    } else if (avg_strategy == 2){
      
      // update encoder vars using an exponentially weighted average
      angleHip = beta*tempAvgHip + (1-beta)*angleHip; 
      angleKne = beta*tempAvgKne + (1-beta)*angleKne; 
      angleAnk = beta*tempAvgAnk + (1-beta)*angleAnk;
    }
  }
  if (displayMsg){printMsg();}
}
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

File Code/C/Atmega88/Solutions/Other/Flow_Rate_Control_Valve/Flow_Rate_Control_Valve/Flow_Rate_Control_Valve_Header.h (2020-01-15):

//Slave Micro Testing Header File

//Include necessary .h files.
#include <stdio.h>
#include <avr/io.h>
#include <avr/interrupt.h>

//Define the clock speed.
#define F_CPU 16000000UL // 16 MHz CPU Clock Frequency
#include <util/delay.h>   // Include the built in Delay Function

//Define pin setting and clearing macros.
#define sbi(var, mask)   ((var) |= (uint8_t)(1 << mask))
#define cbi(var, mask)   ((var) &= (uint8_t)~(1 << mask))

//Define SPIF value (used for SPI communication).
#define SPIF 7

//Define USART Parameters.
#define FOSC F_CPU					//CPU Clock Frequency must be set correctly for the USART to work
//#define BAUD 9600					//BAUD Rate.  Maximum appears to be 921600.
#define BAUD 57600					//BAUD Rate.  Maximum appears to be 921600.
#define MYUBRR FOSC/16/BAUD-1

//Define Robot Parameters.
#define NUM_TOTAL_MUSCLES 24
#define NUM_FRONT_LEG_MUSCLES 6
#define NUM_MULTIPLEXER_PINS 3
#define NUM_PRESSURE_SENSORS 24
#define NUM_POTENTIOMETERS 14
#define NUM_SENSORS_TOTAL 38

//Define Conversion Parameters.
#define NUM_BYTES_PER_FLOAT 4
#define NUM_BYTES_PER_UINT16 2

//Define the necessary structures.
struct int_struct
{
	unsigned int * array;
	unsigned char length;
};

struct float_struct
{
	float * array;
	unsigned char length;
};

struct single_array_struct
{
	unsigned char IDs[38];				//This assumes that there will be <255 muscles, or the ID variable will overflow.
	float values[38];
	unsigned char length;				//This assumes that there will be <255 muscles, or the length variable will overflow.
};

struct int_array_struct
{
	unsigned char IDs[38];				//This assumes that there will be <255 muscles, or the ID variable will overflow.
	uint16_t values[38];			//This assumes that the muscle activation value will be in the range [0, 65535].
	unsigned char length;				//This assumes that there will be <255 muscles, or the length variable will overflow.
};

struct muscle_info_struct 
{
	unsigned char ID;
	unsigned char * port;
	unsigned char pin;
};

struct slave_info_struct
{
	uint8_t muscle_ID;
	uint8_t slave_num;
};


//Type Conversion Functions.
int * int2lowhighbytes(int myint);
unsigned int lowhighbytes2int(unsigned int low_byte, unsigned int high_byte);
uint16_t byte_array2int(unsigned char byte_array[]);
float byte_array2float(unsigned char byte_array[]);
void int2byte_array(uint16_t my_int, unsigned char byte_array[]);
void float2byte_array(float my_float, unsigned char byte_array[]);
float muscle_int2muscle_volt(unsigned int muscle_int);
unsigned int sensor_volt2sensor_int(unsigned int sensor_volt);
uint16_t ADC2uint16( unsigned int ADC_value );
char get_char_bits(char mychar, char no_of_bits);

//Low Level UART Functions.
void uart_putchar(char c, FILE *stream);
unsigned char uart_getchar(void);

//Low Level SPI Functions.
void spi_write(unsigned char spi_data);
unsigned char spi_read( void );
unsigned char spi_read_write(unsigned char spi_data);

//High Level SPI Functions.
void write2slave( uint16_t value_to_write, uint8_t slave_num );
void WriteCommandData2Slaves( struct int_array_struct * command_data_ptr );

//Low Level Pin State Setting Function.
void set_pin_state( unsigned char * port_num, unsigned char pin_num, unsigned char pin_state);

//High Level Serial Write Functions.
void serial_write_start_bytes( void );
void serial_write_end_bytes( void );
void serial_write_string2matlab(char mystring[]);
void serial_write_int2matlab( int myint );
void serial_write_int_array2matlab( int myint_array[], int array_length );
void serial_write_single_array2matlab( float myfloat_array[], int array_length );
void serial_write_sensor_data_ints2matlab( struct int_array_struct * sensor_data_ptr );
void serial_write_sensor_data_singles2matlab( struct single_array_struct * sensor_data_ptr );

//High Level Serial Read Functions.
void wait_for_start_sequence( void );
unsigned int serial_read_matlab_int( void );
struct int_struct serial_read_matlab_int_array( void );
struct float_struct serial_read_matlab_single_array( void );
void serial_read_matlab_muscle_command_ints( struct int_array_struct * command_data_ptr );
void serial_read_matlab_muscle_command_singles( struct single_array_struct * single_array_struct_ptr );

//Setup Functions.
void SetupTimerInterrupts( void );
void SetupUSART( void );
void SetupSPI( void );
void SetupADC( void );
void SetupPins( void );
void SetupMicro( void );

//ADC-DAC Functions.
uint16_t ADC2DAC(uint16_t adc_value);
void write2DAC(unsigned int value_to_write);																						//Medium Level DAC Writing Function.
unsigned int readADC( unsigned int channel_num );																					//Medium Level ADC Reading Function.
void set_multiplexer_channel_with_pins( unsigned char * port_num, unsigned char * pin_nums, unsigned char channel_num );			//Medium Level Multiplexer Channel Setting Function.
void set_multiplexer_channel( unsigned char channel_num );																			//High Level Multiplexer Channel Setting Function.
void GetSensorData( struct int_array_struct * sensor_data_ptr );
unsigned char GetMuscleInfoIndex( unsigned char muscle_ID );
uint8_t GetMuscleIndex( uint8_t muscle_ID_target );
void UpdateMuscleOnOffStates( struct int_array_struct * command_data_ptr);
void UseDACAsMusclePin(struct int_array_struct * command_data_ptr);

//Define the the standard output.
static FILE mystdout = FDEV_SETUP_STREAM(uart_putchar, NULL, _FDEV_SETUP_WRITE);

//Declare global constants.
extern const uint16_t dac_on_value;						//[#] Value to which the dac should be set when the valve manifold is turned on.
extern const uint16_t dac_off_value;
extern const uint8_t window_size;
extern const uint8_t multiplexer_pins1[NUM_MULTIPLEXER_PINS];
extern const uint8_t multiplexer_pins2[NUM_MULTIPLEXER_PINS];
extern const uint8_t * multiplexer_port;
extern const struct muscle_info_struct muscle_info[NUM_FRONT_LEG_MUSCLES];
//extern const struct slave_info_struct slave_info[NUM_FRONT_LEG_MUSCLES];
extern const struct slave_info_struct slave_info[NUM_TOTAL_MUSCLES];

extern const uint16_t activation_threshold;

//Declare global variables.
extern unsigned int dac_data;									//[#] Value to send to dac.
extern unsigned int count;										//[#] Counter for the number of interrupt cycles.
extern unsigned char clock_pin_state;							//[T/F] Clock Pin State.

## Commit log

2019-11-21 Add files via upload
    Tendon tensioner inner spool. First commit by Melissa.
    [AARL_Puppy_18_02_01_011_Tensioner_Inner.SLDPRT]
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2020-01-22 Fixed pot read in GetSensorData.
    The issue turned out to be a hardware problem (broken MUX IC), so code changes were minimal.
    [ADC_DAC_Functions.c]
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2020-02-21 Updated slave pressure tolerance.
    [Slave_Micro_Testing_Main.c]
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2020-03-03 Leg Support Parts1
    Leg support iterations created thus far and other modified parts pertaining to leg attachment.
    [049+050.SLDASM, AARL_Puppy_18_01_01_044.SLDPRT, AARL_Puppy_18_01_01_044.STL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]
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2020-09-30 Leg Parts Proportioned
    The parts that make up the front and hind legs have been adjusted to correspond with the correct leg segment proportions based on the total length of the back (20.75 in)
    [049+050.SLDASM, 22+23.SLDASM, 27+28.SLDASM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]
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2020-10-06 Final Leg Parts
    Deleted some extra files that are old and just confusing
    [AARL_Puppy_18_01_01_002-52+53.SLDASM, AARL_Puppy_18_01_01_003-53+56+57+SlabAssembly.SLDASM, AARL_Puppy_18_01_01_004-54+SlabAssembly.SLDASM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]
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2020-10-07 Added copy of old mechanical CAD directory.
    Attempting to resolve conflicts by temporarily re-instating the old mechanical CAD directory along side the new mechanical CAD directory.
    [116515 DGP-25-G1_8---(F).sldprt, 153327_QSM_6_4.sldprt, 153366 QSMT-4.sldprt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]
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2020-10-13 Shortened long file names.
    [AARL_QR_EL_EN1-amt102-0048-i4000-s.sldasm, AARL_QR_EL_EN1_001-CUI_DEVICES_amt-102-base-rev-k.sldprt, AARL_QR_EL_EN1_002-CUI_DEVICES_amt-102-top-cover-rev-h.sld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]
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2020-10-16 Added inner and outer tensioner files deleted the old inner tensioner file
    [AARL_Puppy_18_02_01_011_Tensioner_Inner.SLDPRT, AARL_Puppy_Tendon_Tensioner_Inner.SLDPRT, AARL_Puppy_Tendon_Tensioner_Outer.SLDPRT]
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2020-10-30 Many updates to the spine.
    New back hip components were designed. Spine muscle attachment points were updated. Central spine components were modified to accept new device mounting.
    [AARL_Puppy_18_01_04_004.SLDASM, AARL_Puppy_18_01_04_043.STL, AARL_Puppy_18_01_06_002.SLDASM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]
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2020-11-25 Fixing fitting attachment.
    [AARL_QR_FR_LE_PA_FL_019.SLDPRT, AARL_QR_PN_FT_008-QSMT-4-Custom.SLDPRT]
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2020-12-09 Updated spine to accomodate new hip muscle fixtures.
    [AARL_QR_EL_EN2-amt102-0048-i6350-s.sldasm, AARL_QR_EL_PA_000-Pressure_Sensor_Array.SLDASM, AARL_QR_EL_PM-Pressure_Sensor_Mounting.SLDASM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]
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2020-12-27 Allow to specify applied currents, fix initial voltage simulation value, create network that matches original CPG from commit 01d32c28846c0f68c4aa41f75724f5375fee945c
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2021-03-24 Updated slave SPI code to match master SPI updates and added encoder read code.
    [Encoder_Documentation.xlsx, Slave_Info_Documentation.xlsx]
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2021-05-04 Ground Update 2
    Fixed Overlapping issue - Updated geometry and trajectory (Half Ellipse)
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2021-06-21 Collected data
    Heat set insert testing and collected data from Muscle Mutt
    [Heat_set.SLDPRT, Heat_set.STL, Heat_set_V2.SLDPRT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]
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2021-08-10 Adjustments to Prevent Pulley Interference
    [AARL_QR_FR_LE_PL_BL_006_v2(003).SLDPRT]
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2021-09-28 Significant reorganization of Emma's changes.
    - Any remaining temporary files were deleted.
    - Changes that existed in my InProgress folders were moved to InProgress folders for Emma.
    - Deleted excess parts.
    [6389K352_LIGHT DUTY DRY-RUNNING SLEEVE BEARING.SLDPRT, 91251A191_BLACK-OXIDE ALLOY STEEL SOCKET HEAD CAP SCREW (1).SLDPRT, 93365A110_HEAT-SET INSERTS FOR PLAST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]
2021-09-28 Reorganized Manuel's changes to better fit the directory structure.
    - Temporary files deleted.
    - Parts moved to: \GitHub\Quadruped_Robot\CAD_Mechanical\AARL_QR-Quadruped\AARL_QR_FR-Frame\InProgress\Manuel
    [AARL_QR_FR_BO_012.1.1.SLDPRT, AARL_QR_FR_BO_012.1.SLDPRT, AARL_QR_FR_BO_012.3.1.SLDPRT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]
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2021-10-04 Fixing BPA muscle interpolation.
    - Created strain, force, and pressure interpolants.
    - Created strain, force, and pressure field plots.
    - Need to plot interpolant results.
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2022-01-12 -Added project code for both force sensing and Quadruped Test Bench. -Added documentation for Voltage Divider Board PCB.
    [6in1.brd, 6in1.sch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]
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2022-01-26 Several pernicious bug fixes.
    [debugging_check_list.xlsx]
2022-01-26 more changes
    continue making changes and tubing organizers for the quadruped puppy.
    [AARL_TUBE_ARRANGEMENT.SLDPRT, AARL_TUBE_ARRANGEMENT.STL, AARL_TUBING.SLDPRT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]
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2022-02-01 Attempting to fix conflict.
    [Hill_Muscle_Data.xlsx, debugging_check_list.xlsx]
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2022-02-09 Multistate oscillator fully translated into objected oriented framework.
    [Neuron_Data.xlsx]
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2022-03-06 parasolid files
    biarticular parasolid files will be able to open in SW2020
    [AARL_BA_HIP_JOINT.SLDPRT, AARL_BA_HIP_JOINT.STEP, AARL_BA_HIP_JOINT.x_t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]
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2022-07-07 Modified angle reading program and deleted noise testing program
    Modifications: Removed while loop and consolidated program flow control in loop()
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2022-07-08 Modified treadmill model
    Made upgrades to the CAD model of the treadmill including added handmade square part and mated more things
    [2755_1_12.sldprt, 2755_1_14.sldprt, 2755_1_18part.SLDPRT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]
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2022-07-11 Added some final features to treadmill
    New bar and attachment as well as pulleys
    [2100_slideInHanger.SLDPRT, 2755_1_wheels_maybe_right.SLDASM, 27inpipe.SLDPRT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]
2022-07-12 Added pulleys and chain subassembly
    Put in fixed pulleys
    [2755_1_wheels_maybe_right.SLDASM, 2Pulley_and_chain_subassembly.SLDASM, 3213T57_Pulley.SLDPRT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]
2022-07-12 Finished Treadmill model
    Added the board for the treadmill, two axels, motor holding shelf, some parts of the harness, and the treadmill band. Finished the model
    [17inPole.SLDPRT, 2534T21_Clamp-on Framing Fitting.SLDPRT, 2755_1_wheels_maybe_right.SLDASM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]
2022-07-20 Fixed bugs in leg extension
2022-07-27 Built string clamp for keeping the tendon strings from slipping
    Clamp assembly is called thick bars sabrina clamp assem and it consists of not skinny bars new chompy thingy and for thick bars top. I'll change the names sometime. Other things are the bobs which are a scrapped testing device and I will delete later.
    [8020- 1515-UL X 145_25in.SLDPRT, 8020- 1515-UL X 145_57.5in.SLDPRT, 8020- 1515-UL X 145_78in.SLDPRT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]
2022-07-27 Revert "Built string clamp for keeping the tendon strings from slipping"
    This reverts commit d66a15a83d24bde9dcf45b4c6517efcf8b44beac.
    [8020- 1515-UL X 145_25in.SLDPRT, 8020- 1515-UL X 145_57.5in.SLDPRT, 8020- 1515-UL X 145_78in.SLDPRT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]
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2022-08-01 Put my files that were in the wrong folder into the github folder under Clara, created new file, edited serpentine clamp assembly
    attempted to smush the serpentine clamp (Sabrina clampy thingy assembly) into the THIS ONE editable knee with mods, created just the file for a new part called lasso stopper
    [2_For_thick_bars_top_of_sabrina.STL, 2_Not_skinny_bars_new_chompy_thingy.STL, 2nd Knee Joint my copy.SLDPRT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]
2022-08-03 deleted unnecessary files, made changes to dowel system
    deleted old knee parts that were not editable or incorrect model, created a dowel first draft (lasso stopper burger)
    [2nd Knee Joint my copy.SLDPRT, Assem1.SLDASM, FOR_PRINT_Lasso_stopper_burger.STL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]
2022-08-03 added sabrina's files as stls to my folder for printing
    added revised dowels
    [twistyEndTendon-SabrinaMc-hdw[10].STL, twistyEndTendon-SabrinaMc-hdw[11]biggerrevs.STL]
2022-08-09 Create intergratedTwistyTest-SabrinaMc-hdw.SLDPRT
    Created this to test how to integrate the twisty thing into the quadruped.
    [intergratedTwistyTest-SabrinaMc-hdw.SLDPRT]
2022-08-10 Made tslot attachment assembly for printing
    Nearly finished an attachment for the testing mechanism that slides into a t slot and allows us to test one of our ideas
    [Example_flush_wraparound.SLDPRT, Lasso_stopper_burger.SLDPRT, TslotAttachmentAssem.SLDASM]
2022-08-10 saved t slot attachment as STL
    Finished t slot attachment and saved as STL for printing
    [CopyforSTLPart1^TslotAttachmentAssem[14]mightHaveReadOnlyThings.STL, FINALcopyforSTLPart1^TslotAttachmentAssem[14]mightHaveReadOnlyThings.STL, FINALstlActualPa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]
2022-08-12 added treadmill files from non github folder to github folder, resaved some string attachment pieces.
    saved some copies of our dowel and integrated dowel as stls and got rid of hole on implemented dowel. Added files from originally seperate folder called test bench solidworks files to a github folder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
    [2751_1.SLDASM, 27inpipe.SLDPRT, 2holesattachment.SLDPRT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]
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2024-03-01 2nd order approximations
    it doesn't work
    [BigPulleyAdapter.SLDPRT, LargePulley.SLDASM, M3_Screw.SLDPRT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]
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2024-07-31 Made Bushings for bearing and made redesigned pulley for testing
    [258mmlegonyxspringankleSTL.STL, 729lipOnyx_Spring_Ankle.SLDPRT, circleshaftbushing675mm731.STL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]
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

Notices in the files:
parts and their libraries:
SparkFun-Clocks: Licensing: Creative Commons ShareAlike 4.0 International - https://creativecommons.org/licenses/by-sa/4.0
